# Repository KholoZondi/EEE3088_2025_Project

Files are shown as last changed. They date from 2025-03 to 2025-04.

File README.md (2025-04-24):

The repo stores all the shared work between EEE3088F Group 58 members Kholofelo Zondi and Max Mendelow for the Micro-mouse project project 2025. 

This includes the datasheets for certain ICs, past designs, general personal notes, downloaded schematics and the final design with Gerber and production files.

For the final design of the power subsystem, please navigate to "Micro_mouse_circuit/Micro_mouse_final" and consider the contents of the folder "Micro_mouse final" 
as the final design as of April 9th 2025. 

Full names and student numbers
Kholofelo Zondi ZNDKHO003
Max Mendelow MNDMAX003

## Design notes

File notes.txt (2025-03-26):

general q's:
where are the drill holes?
	-all the yellow filled circles

what input are we getting since motors are bidirectional
are the auxillary motors for steering
	-they are currently immaginary. For the time being, we will only be physically connecting 2 motos but we are adding in the capacity to connect 2 more future motors

clarrify requirement 7, 3v3 in?
	-similar to breadboard power sub system - just need to provide output 	pins

report:
block diagram: transfer behaviour shown in blocks and signals ( 3v3 input, DC ) shown with lines 

interface diagram: analogous to programming: shows what are data types passed into and out of function
with hardware - need to show what voltages go in and out, what signals, etc

bread board memo:

boost converter since linear voltage regulators have a minimum input that they regulate from

each motor has 2 physical connectors

check if A0,A1 addresses are correct based on master slave relation
are our board economic for preffered

battery - ina - charg - switch - rest of circuit

2 states: On+charge | off+charge

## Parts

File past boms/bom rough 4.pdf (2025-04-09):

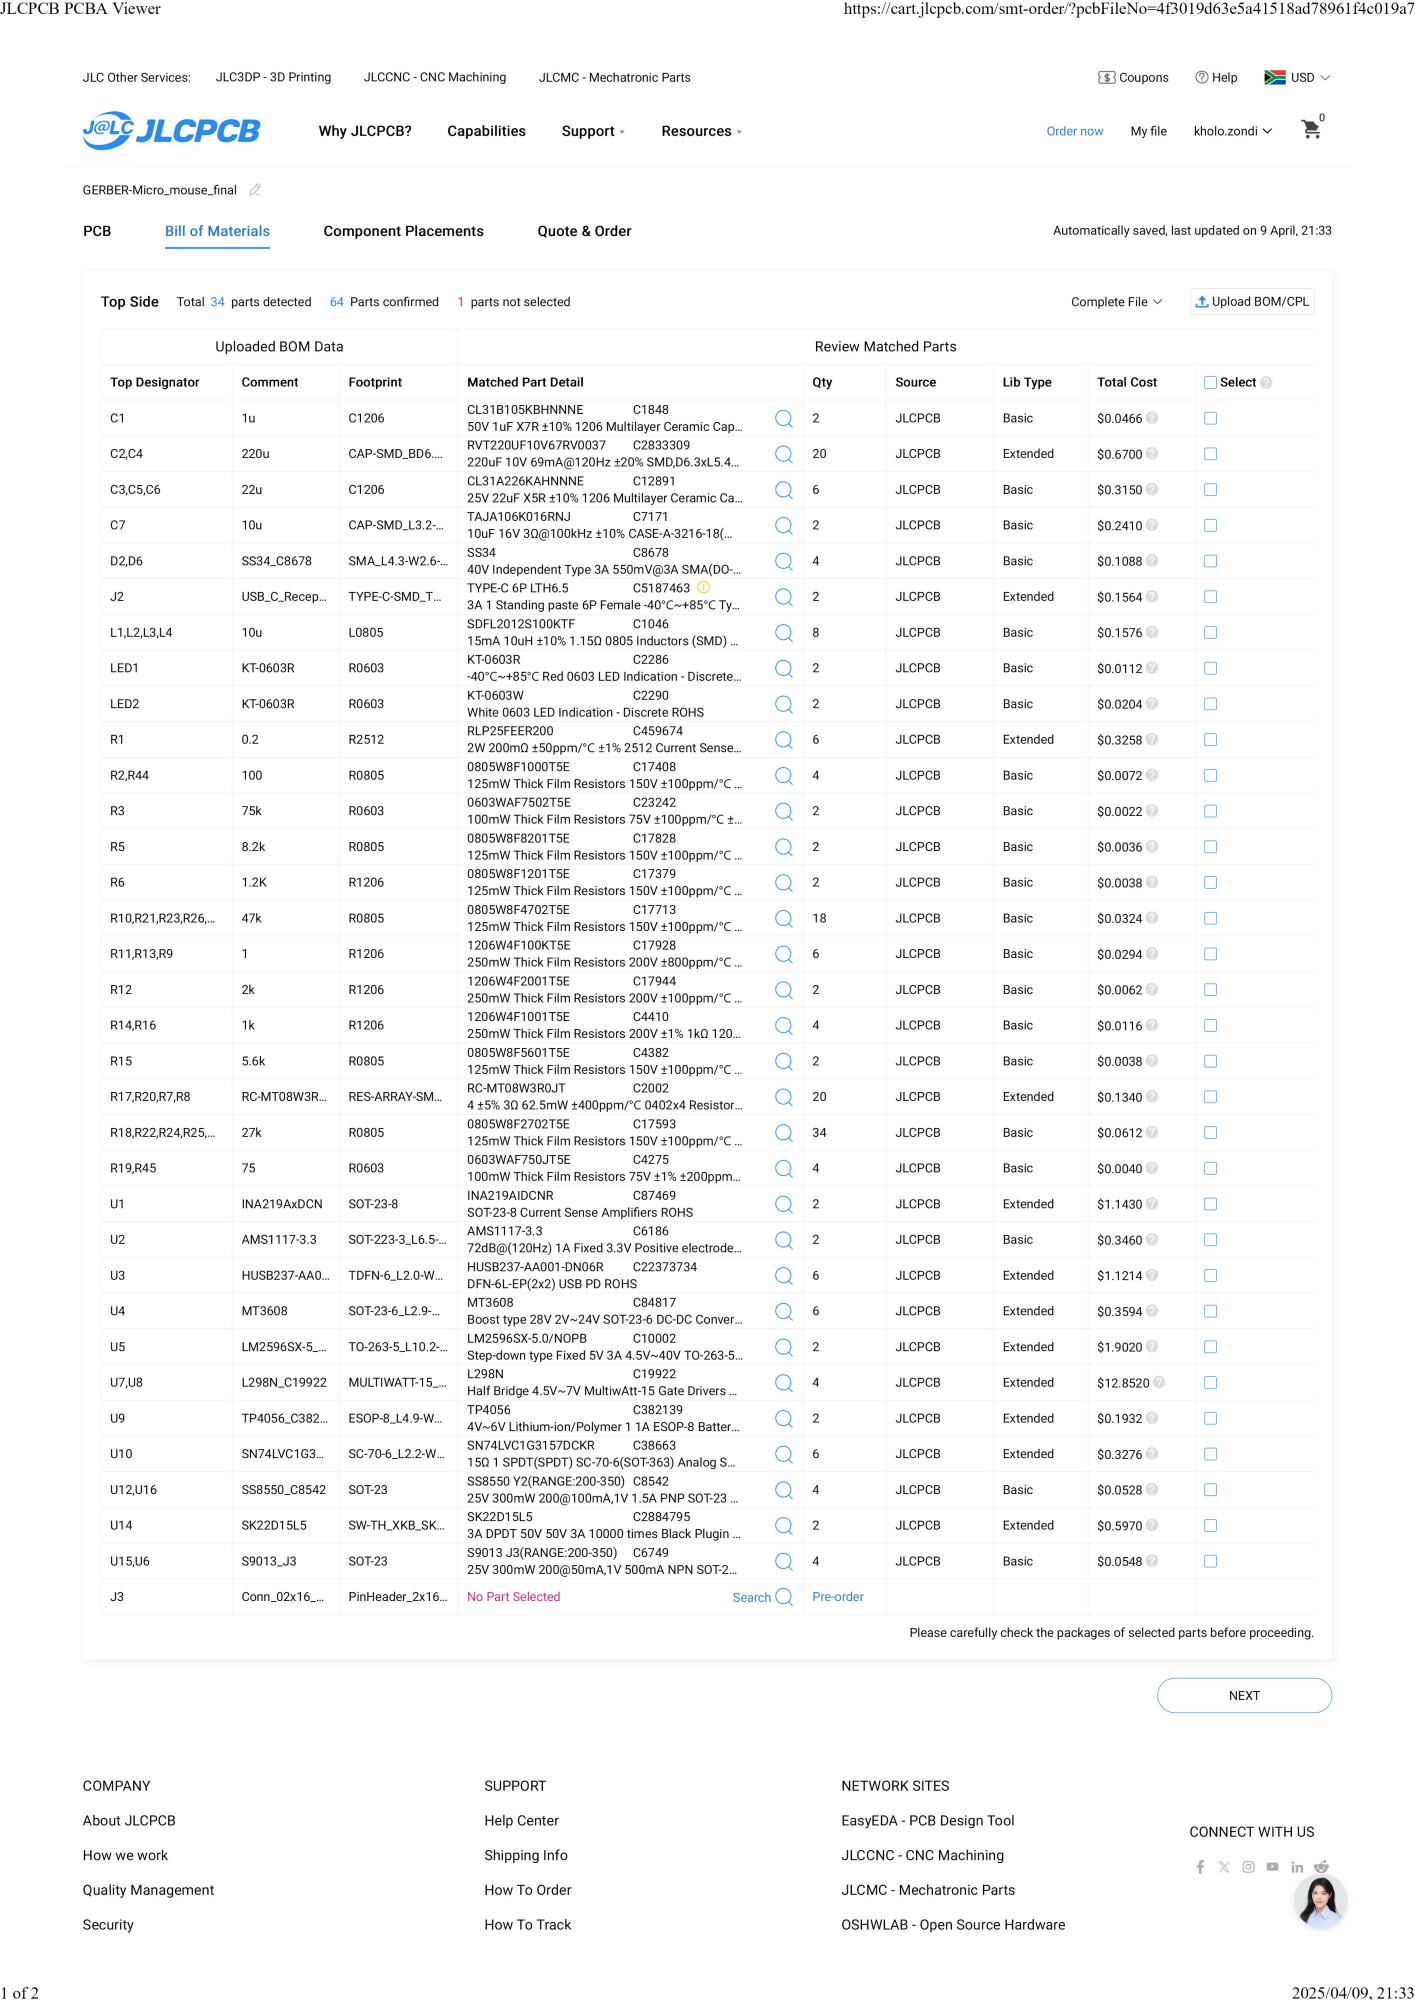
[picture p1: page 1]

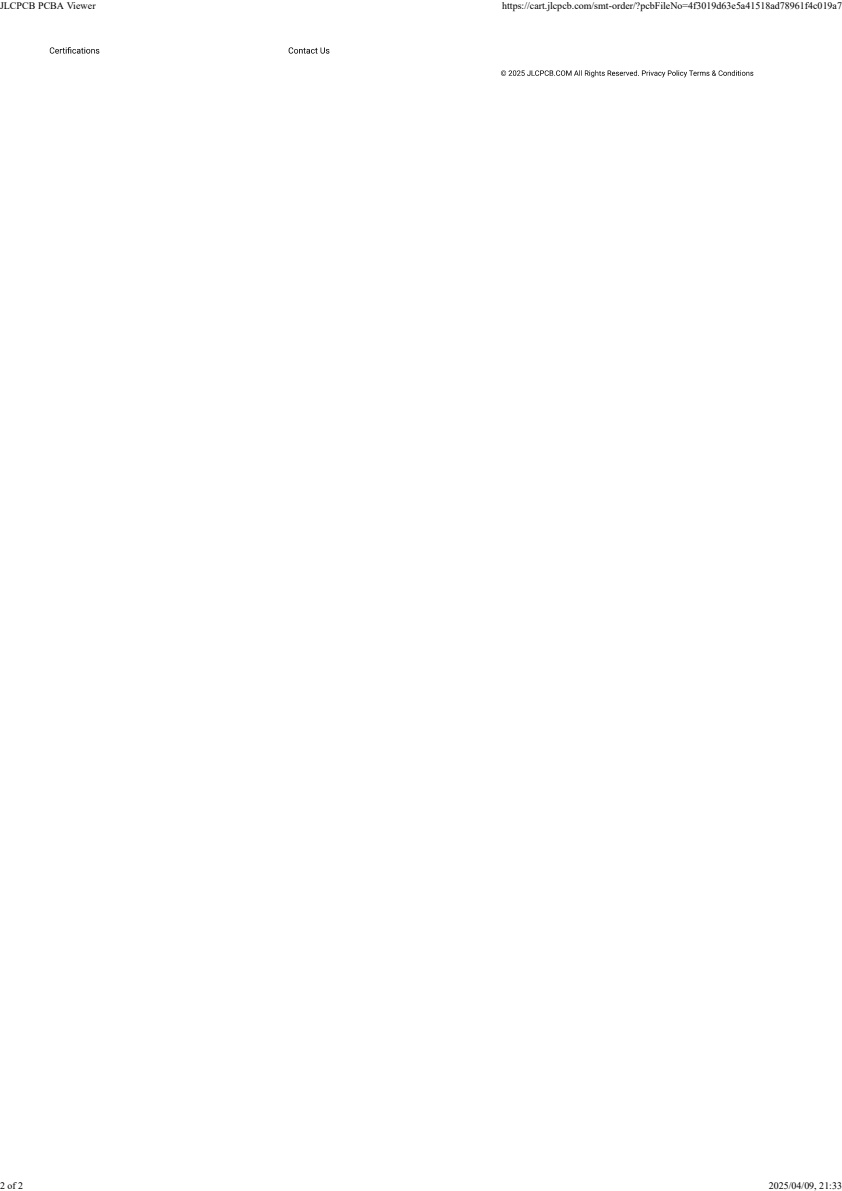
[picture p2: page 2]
JLCPCB PCBA Viewer; https://cart.jlcpcb.com/smt-order/?pcbFileNo=4f3019d63e5a41518ad78961f4c019a7

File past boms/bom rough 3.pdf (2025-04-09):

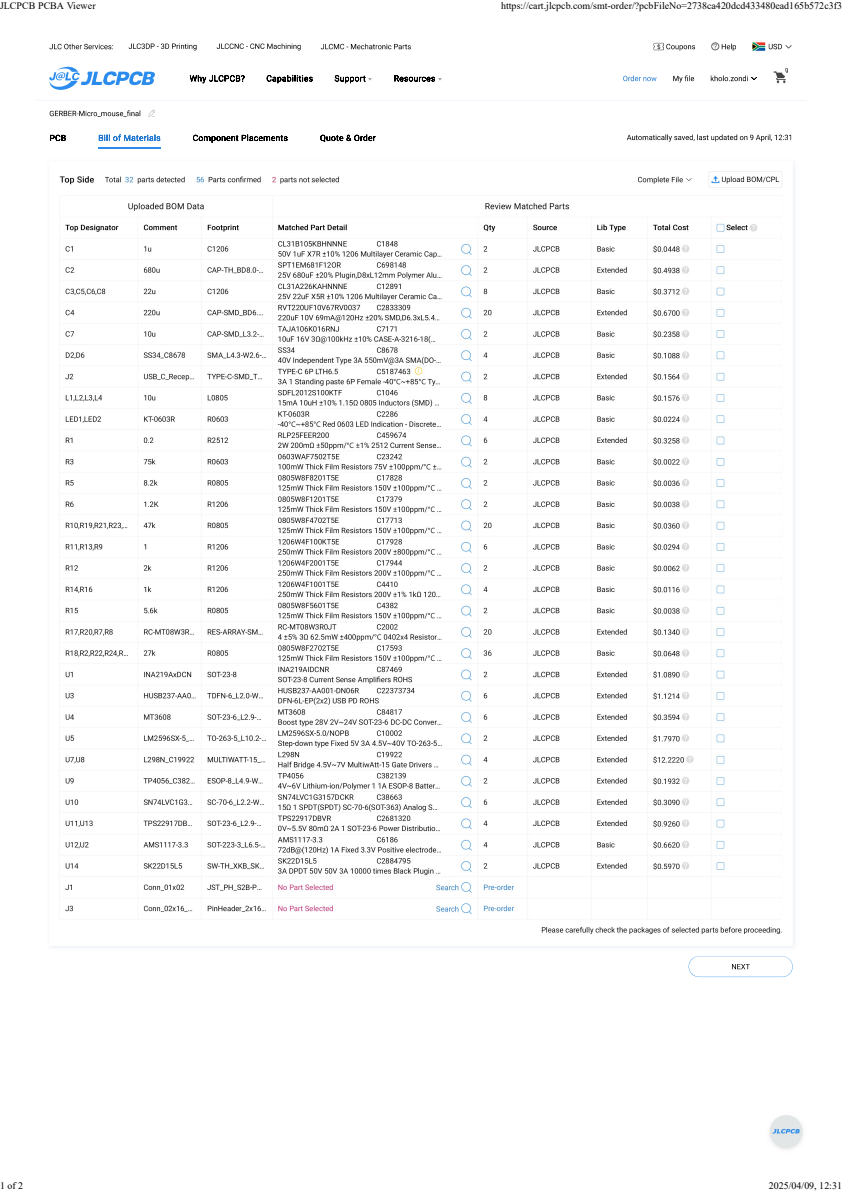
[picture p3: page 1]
JLCPCB PCBA Viewer; https://cart.jlcpcb.com/smt-order/?pcbFileNo=2738ca420dcd433480ead165b572c3f3

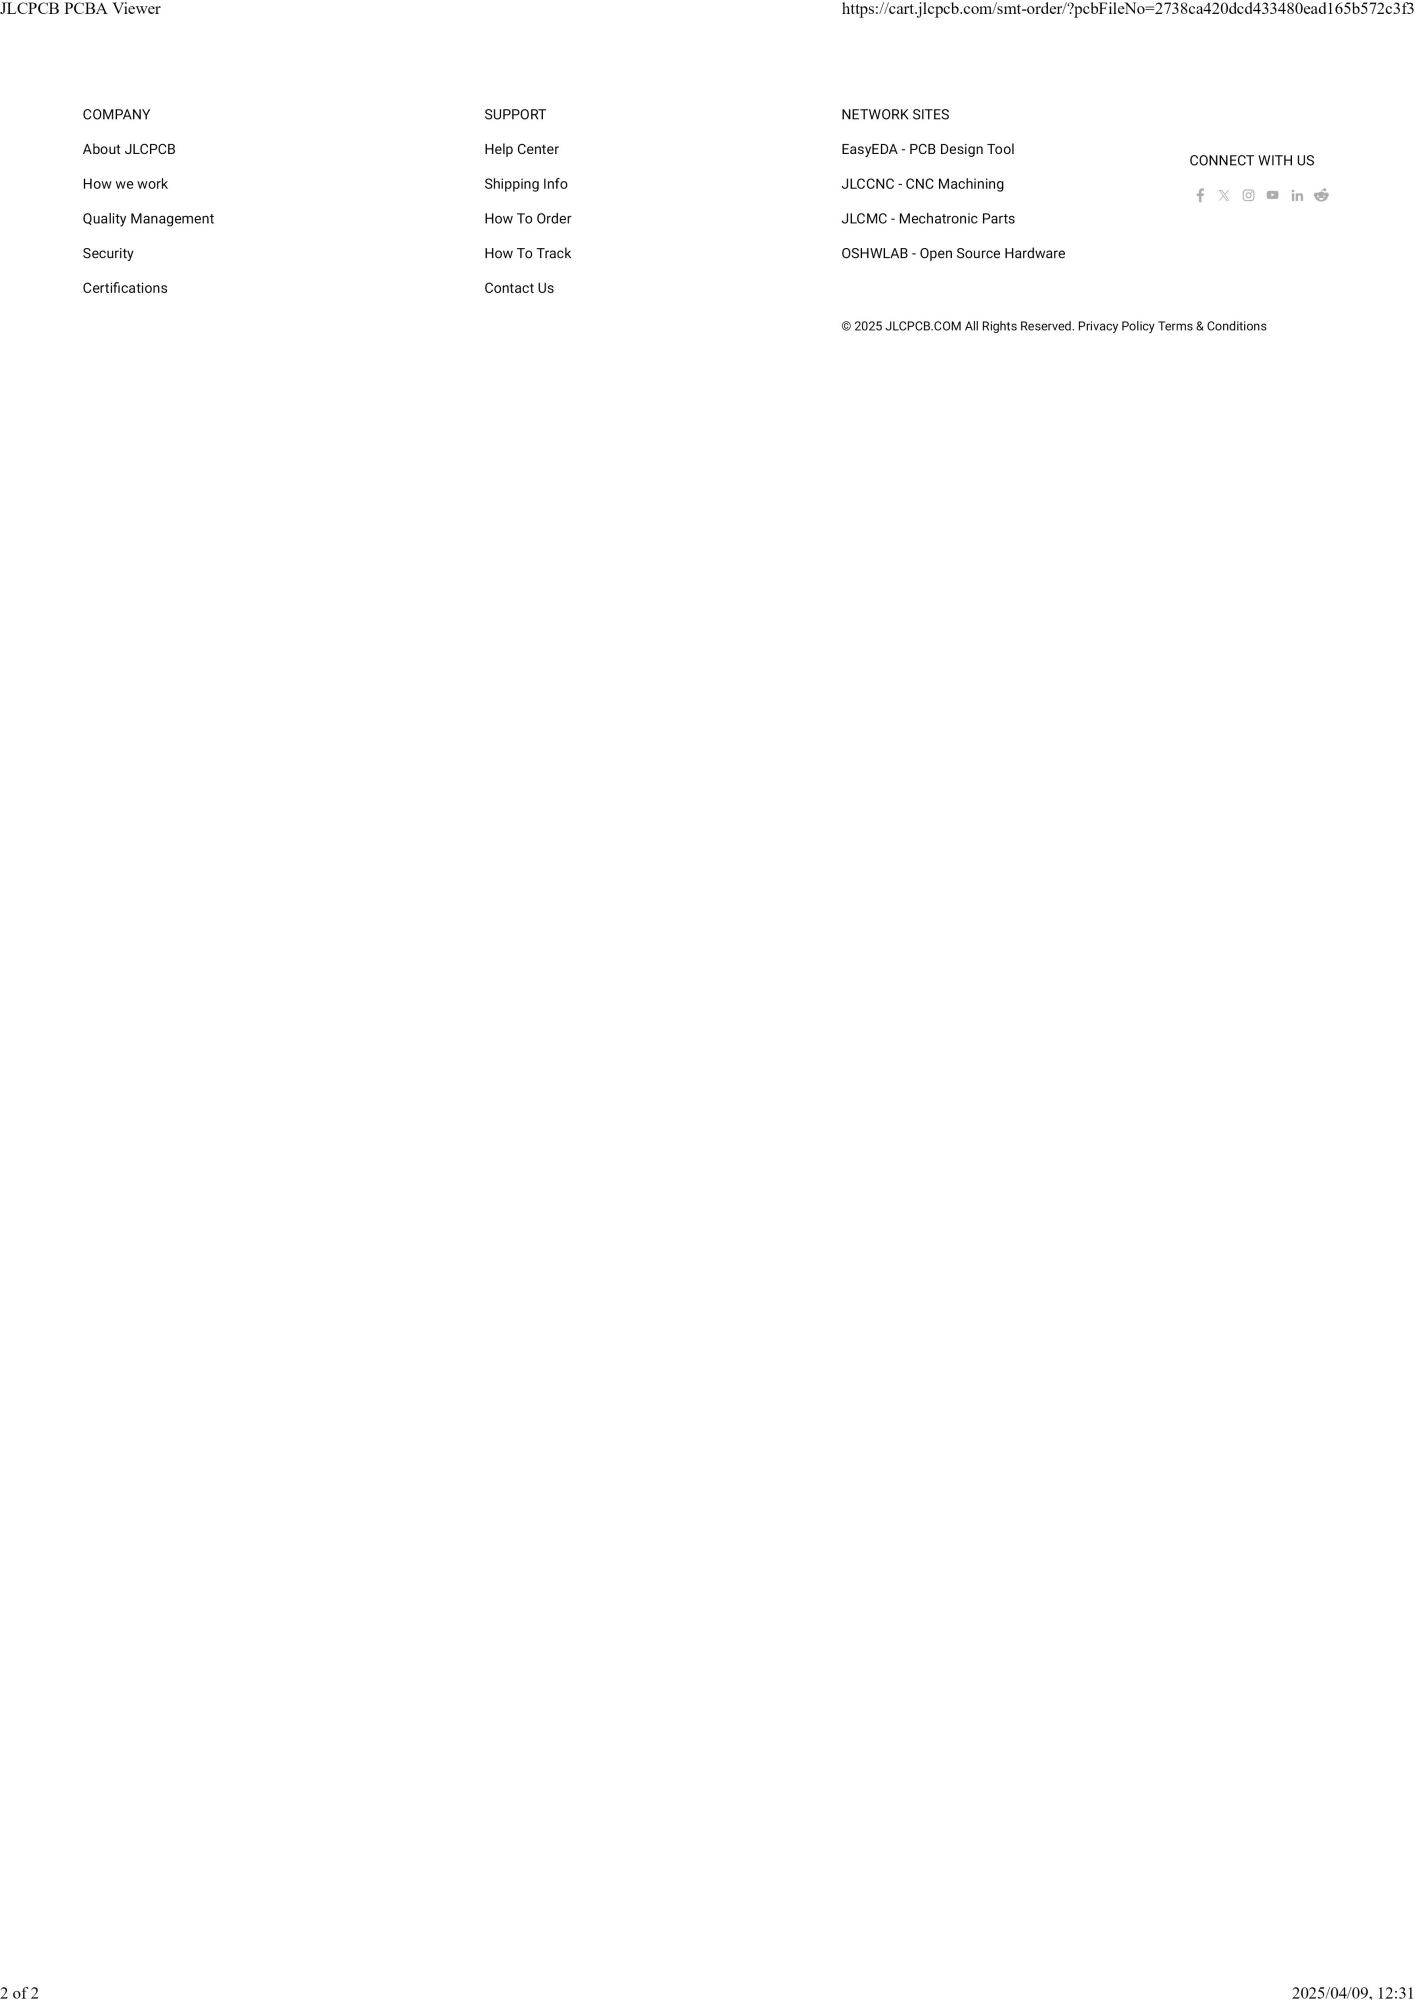
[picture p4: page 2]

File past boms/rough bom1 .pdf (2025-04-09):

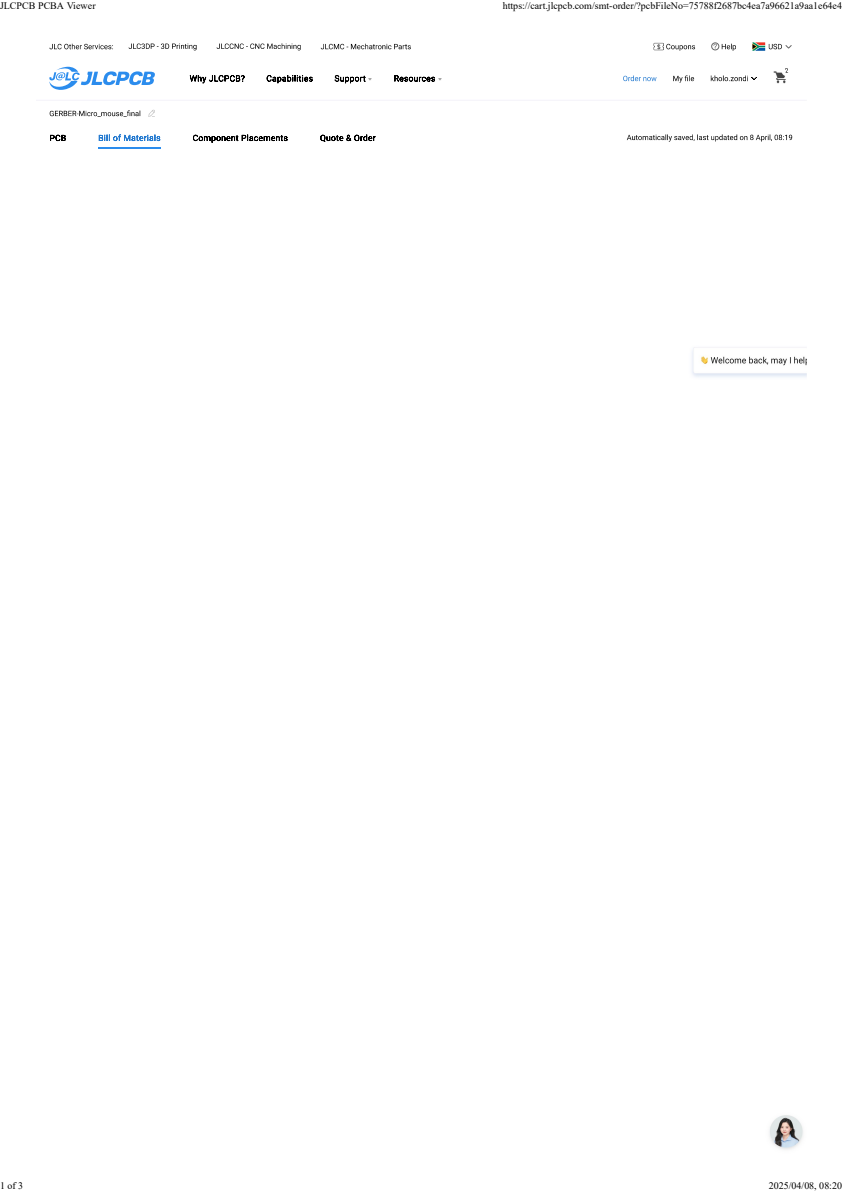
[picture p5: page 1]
JLCPCB PCBA Viewer; https://cart.jlcpcb.com/smt-order/?pcbFileNo=75788f2687bc4ea7a96621a9aa1e64e4

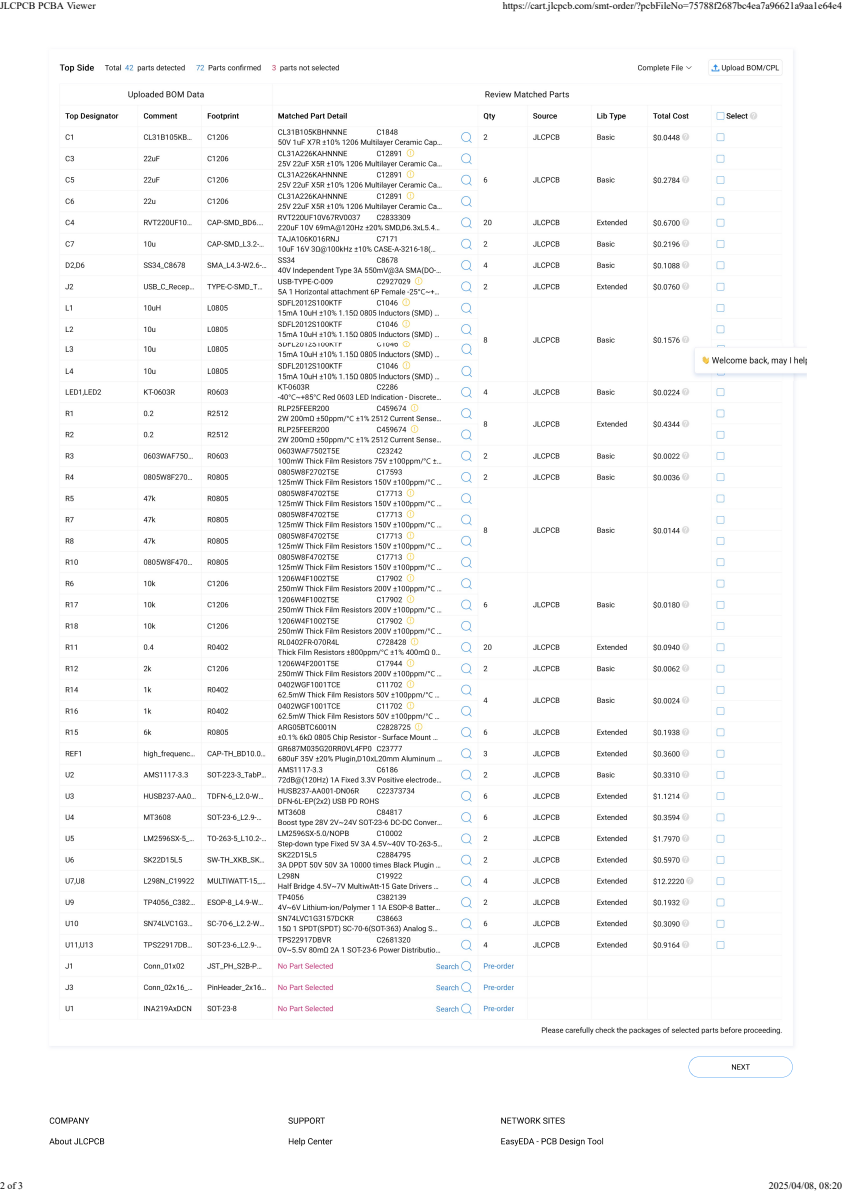
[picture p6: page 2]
JLCPCB PCBA Viewer; https://cart.jlcpcb.com/smt-order/?pcbFileNo=75788f2687bc4ea7a96621a9aa1e64e4

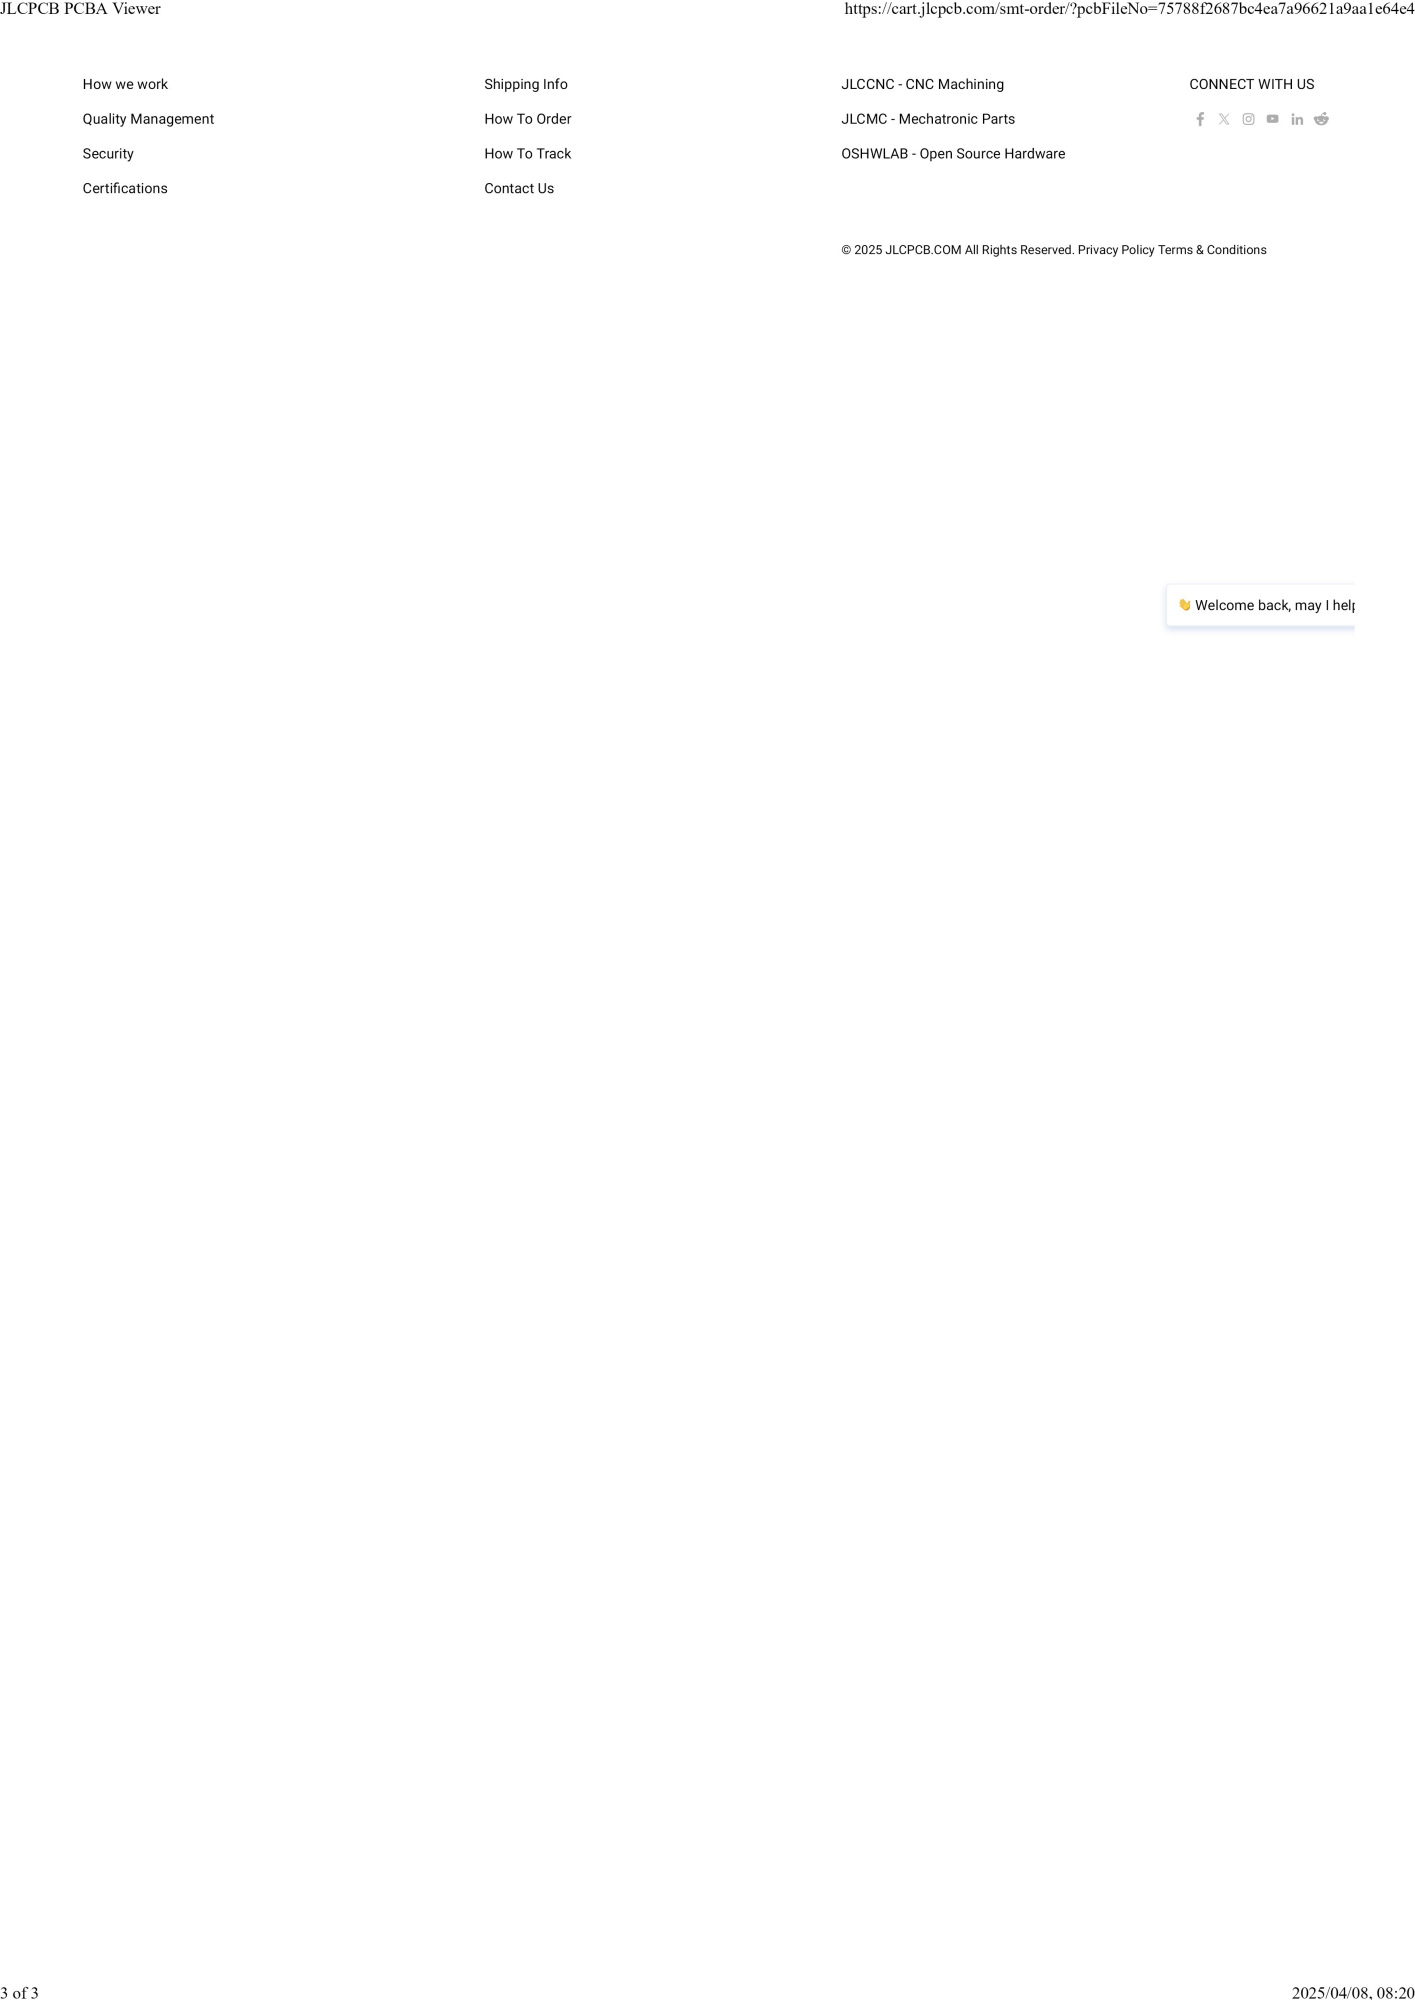
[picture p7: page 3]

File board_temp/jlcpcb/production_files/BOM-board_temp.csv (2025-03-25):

Comment | Designator | Footprint | LCSC | Quantity
IP2721 | U1 | TSSOP-16_4.4x5mm_P0.65mm |  | 1

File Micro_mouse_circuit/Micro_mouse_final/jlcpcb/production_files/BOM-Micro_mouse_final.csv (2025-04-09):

Comment | Designator | Footprint | LCSC | Quantity
LM2596SX-5_0/NOPB | U5 | TO-263-5_L10.2-W8.9-P1.70-TL | C10002 | 1
10u | L1,L2,L3,L4 | L0805 | C1046 | 4
22u | C3,C5,C6 | C1206 | C12891 | 3
1.2K | R6 | R1206 | C17379 | 1
100 | R2,R44 | R0805 | C17408 | 2
27k | R18,R22,R24,R25,R27,R28,R30,R31,R33,R34,R36,R37,R39,R4,R40,R42,R43 | R0805 | C17593 | 17
47k | R10,R21,R23,R26,R29,R32,R35,R38,R41 | R0805 | C17713 | 9
8.2k | R5 | R0805 | C17828 | 1
1 | R11,R13,R9 | R1206 | C17928 | 3
2k | R12 | R1206 | C17944 | 1
1u | C1 | C1206 | C1848 | 1
L298N_C19922 | U7,U8 | MULTIWATT-15_L19.6-W5.0-P1.27-L | C19922 | 2
RC-MT08W3R0JT | R17,R20,R7,R8 | RES-ARRAY-SMD_0402-8P-L2.0-W1.0-BL | C2002 | 4
HUSB237-AA001-DN06R | U3 | TDFN-6_L2.0-W2.0-P0.65-TL-EP | C22373734 | 1
KT-0603R | LED1 | R0603 | C2286 | 1
KT-0603R | LED2 | R0603 | C2290 | 1
75k | R3 | R0603 | C23242 | 1
220u | C2,C4 | CAP-SMD_BD6.3-L6.6-W6.6-FD | C2833309 | 2
SK22D15L5 | U14 | SW-TH_XKB_SK22D15L7 | C2884795 | 1
TP4056_C382139 | U9 | ESOP-8_L4.9-W3.9-P1.27-LS6.0-BL-EP | C382139 | 1
SN74LVC1G3157DCKR | U10 | SC-70-6_L2.2-W1.3-P0.65-LS2.1-BR | C38663 | 1
75 | R19,R45 | R0603 | C4275 | 2
5.6k | R15 | R0805 | C4382 | 1
1k | R14,R16 | R1206 | C4410 | 2
0.2 | R1 | R2512 | C459674 | 1
USB_C_Receptacle_PowerOnly_6P | J2 | TYPE-C-SMD_TYPE-C-6P | C5187463 | 1
AMS1117-3.3 | U2 | SOT-223-3_L6.5-W3.4-P2.30-LS7.0-BR | C6186 | 1
S9013_J3 | U15,U6 | SOT-23 | C6749 | 2
10u | C7 | CAP-SMD_L3.2-W1.6-RD-C7171 | C7171 | 1
MT3608 | U4 | SOT-23-6_L2.9-W1.6-P0.95-LS2.8-BL | C84817 | 1
SS8550_C8542 | U12,U16 | SOT-23 | C8542 | 2
SS34_C8678 | D2,D6 | SMA_L4.3-W2.6-LS5.2-RD | C8678 | 2
INA219AxDCN | U1 | SOT-23-8 | C87469 | 1
Conn_02x16_Odd_Even | J3 | PinHeader_2x16_P2.54mm_Vertical |  | 1
TestPoint_2Pole | TP8 | TestPoint_2Pads_Pitch2.54mm_Drill0.8mm |  | 1
TestPoint_2Pole | TP6 | TestPoint_2Pads_Pitch2.54mm_Drill0.8mm |  | 1
TestPoint | TP1 | TestPoint_Pad_2.5x2.5mm |  | 1
TestPoint_2Pole | TP10 | TestPoint_2Pads_Pitch2.54mm_Drill0.8mm |  | 1
TestPoint_2Pole | TP3 | TestPoint_2Pads_Pitch2.54mm_Drill0.8mm |  | 1
TestPoint | TP18 | TestPoint_Pad_2.5x2.5mm |  | 1
TestPoint | TP17 | TestPoint_Pad_2.5x2.5mm |  | 1
TestPoint | TP16 | TestPoint_Pad_2.5x2.5mm |  | 1
TestPoint | TP15 | TestPoint_Pad_2.5x2.5mm |  | 1
TestPoint | TP14 | TestPoint_Pad_2.5x2.5mm |  | 1
TestPoint | TP13 | TestPoint_Pad_2.5x2.5mm |  | 1
TestPoint | TP12 | TestPoint_Pad_2.5x2.5mm |  | 1
TestPoint | TP11 | TestPoint_Pad_2.5x2.5mm |  | 1
TestPoint_2Pole | TP5 | TestPoint_2Pads_Pitch2.54mm_Drill0.8mm |  | 1
TestPoint_2Pole | TP4 | TestPoint_2Pads_Pitch2.54mm_Drill0.8mm |  | 1
TestPoint | TP20 | TestPoint_Pad_2.5x2.5mm |  | 1
TestPoint | TP19 | TestPoint_Pad_2.5x2.5mm |  | 1

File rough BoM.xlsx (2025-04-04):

Secction |  |  |  |  |  | most likely needed
battery |  |  |  |  |  | boost converter (battery)
requirement | component | model # | base cost (USD) | extended? (+$3) | link (JLC) | linear regulator (battery) (type LDO)
2 | INA219 | INA219AIDCNR | 0.5955 | 3 | https://jlcpcb.com/partdetail/TexasInstruments-INA219AIDCNR/C87469 | h bridge IC (motors)
5 | USB C header /6b | TYPE-C 6P LTH6.5 | 0.0782 | 3 | https://jlcpcb.com/partdetail/ShouHan-TYPE_C_6P_LTH65/C5187463 | usb type c header (battery) | + usb type c pd (battery)
5 | USB C PD | HUSB237 | 0.19 | 3 | https://jlcpcb.com/partdetail/Hynetek-HUSB237_AA001DN06R/C22373734 | INA219 (battery)
3,4 | Charging | TP4056 | 0.09 | 3 | https://jlcpcb.com/partdetail/TPOWER-TP4056/C382139 | Li battery charger
3,4 | Buck dc-dc | LM2596SX-5.0/NOPB | 0.9135 | 0 | https://jlcpcb.com/partdetail/TexasInstruments-LM2596SX_5_0NOPB/C10002
4 | analog switch | SN74LVC1G3157DCKR | 0.0513 | 3 | https://jlcpcb.com/partdetail/TexasInstruments-SN74LVC1G3157DCKR/C38663
2 | shunt resistor | RLP25FEER200 | 0.05 | 3 | https://jlcpcb.com/partdetail/ta_iTech-RLP25FEER200/C459674
Discrete components
 | cap (5V boosted) | CL31A226KAHNNNE |  | 0 | https://jlcpcb.com/partdetail/13537-CL31A226KAHNNNE/C12891
 | 10k resistor | 1206W4F1002T5E |  | 0 | https://jlcpcb.com/partdetail/18590-1206W4F1002T5E/C17902
Sub-total |  |  | 19.9685
Motors
requirement | component | model # | cost (USD) | extended? (+$3) | link (JLC)
8 | On/Off switch | SK22D15L5 | 0.31 | 3 | https://jlcpcb.com/partdetail/XkbConnection-SK22D15L5/C2884795
 | 5V out | MT3608 | 0.06 | 3 | https://jlcpcb.com/partdetail/xi_an_AerosemiTech-MT3608/C84817
Sub-total |  |  | 6.37
Total |  |  | 26.3385
Budget |  |  | 56.5
Left over |  |  | 30.1615

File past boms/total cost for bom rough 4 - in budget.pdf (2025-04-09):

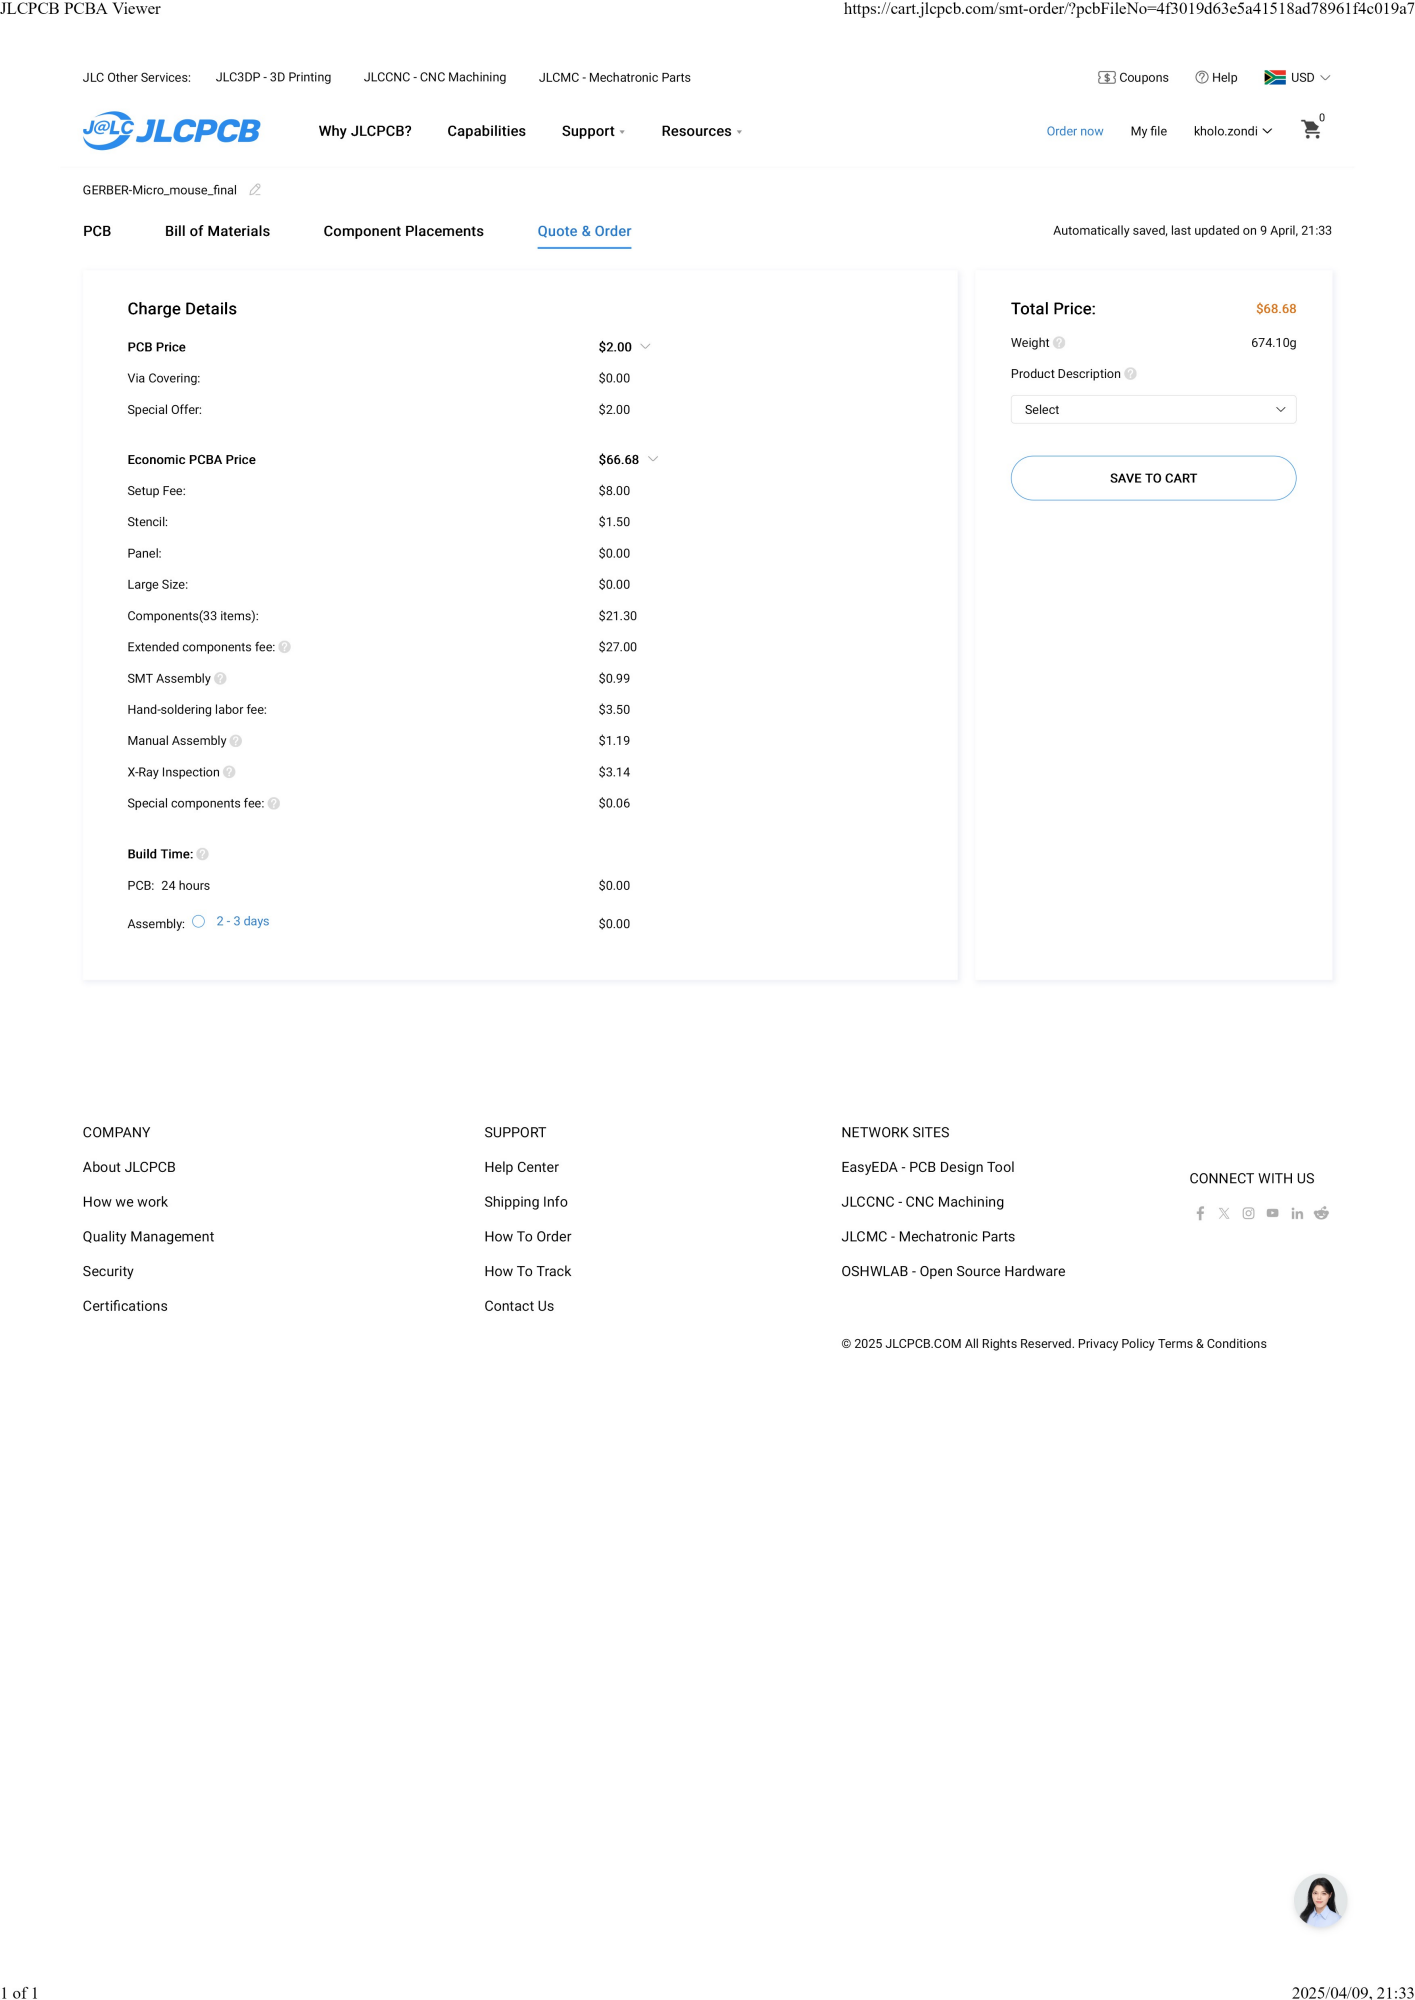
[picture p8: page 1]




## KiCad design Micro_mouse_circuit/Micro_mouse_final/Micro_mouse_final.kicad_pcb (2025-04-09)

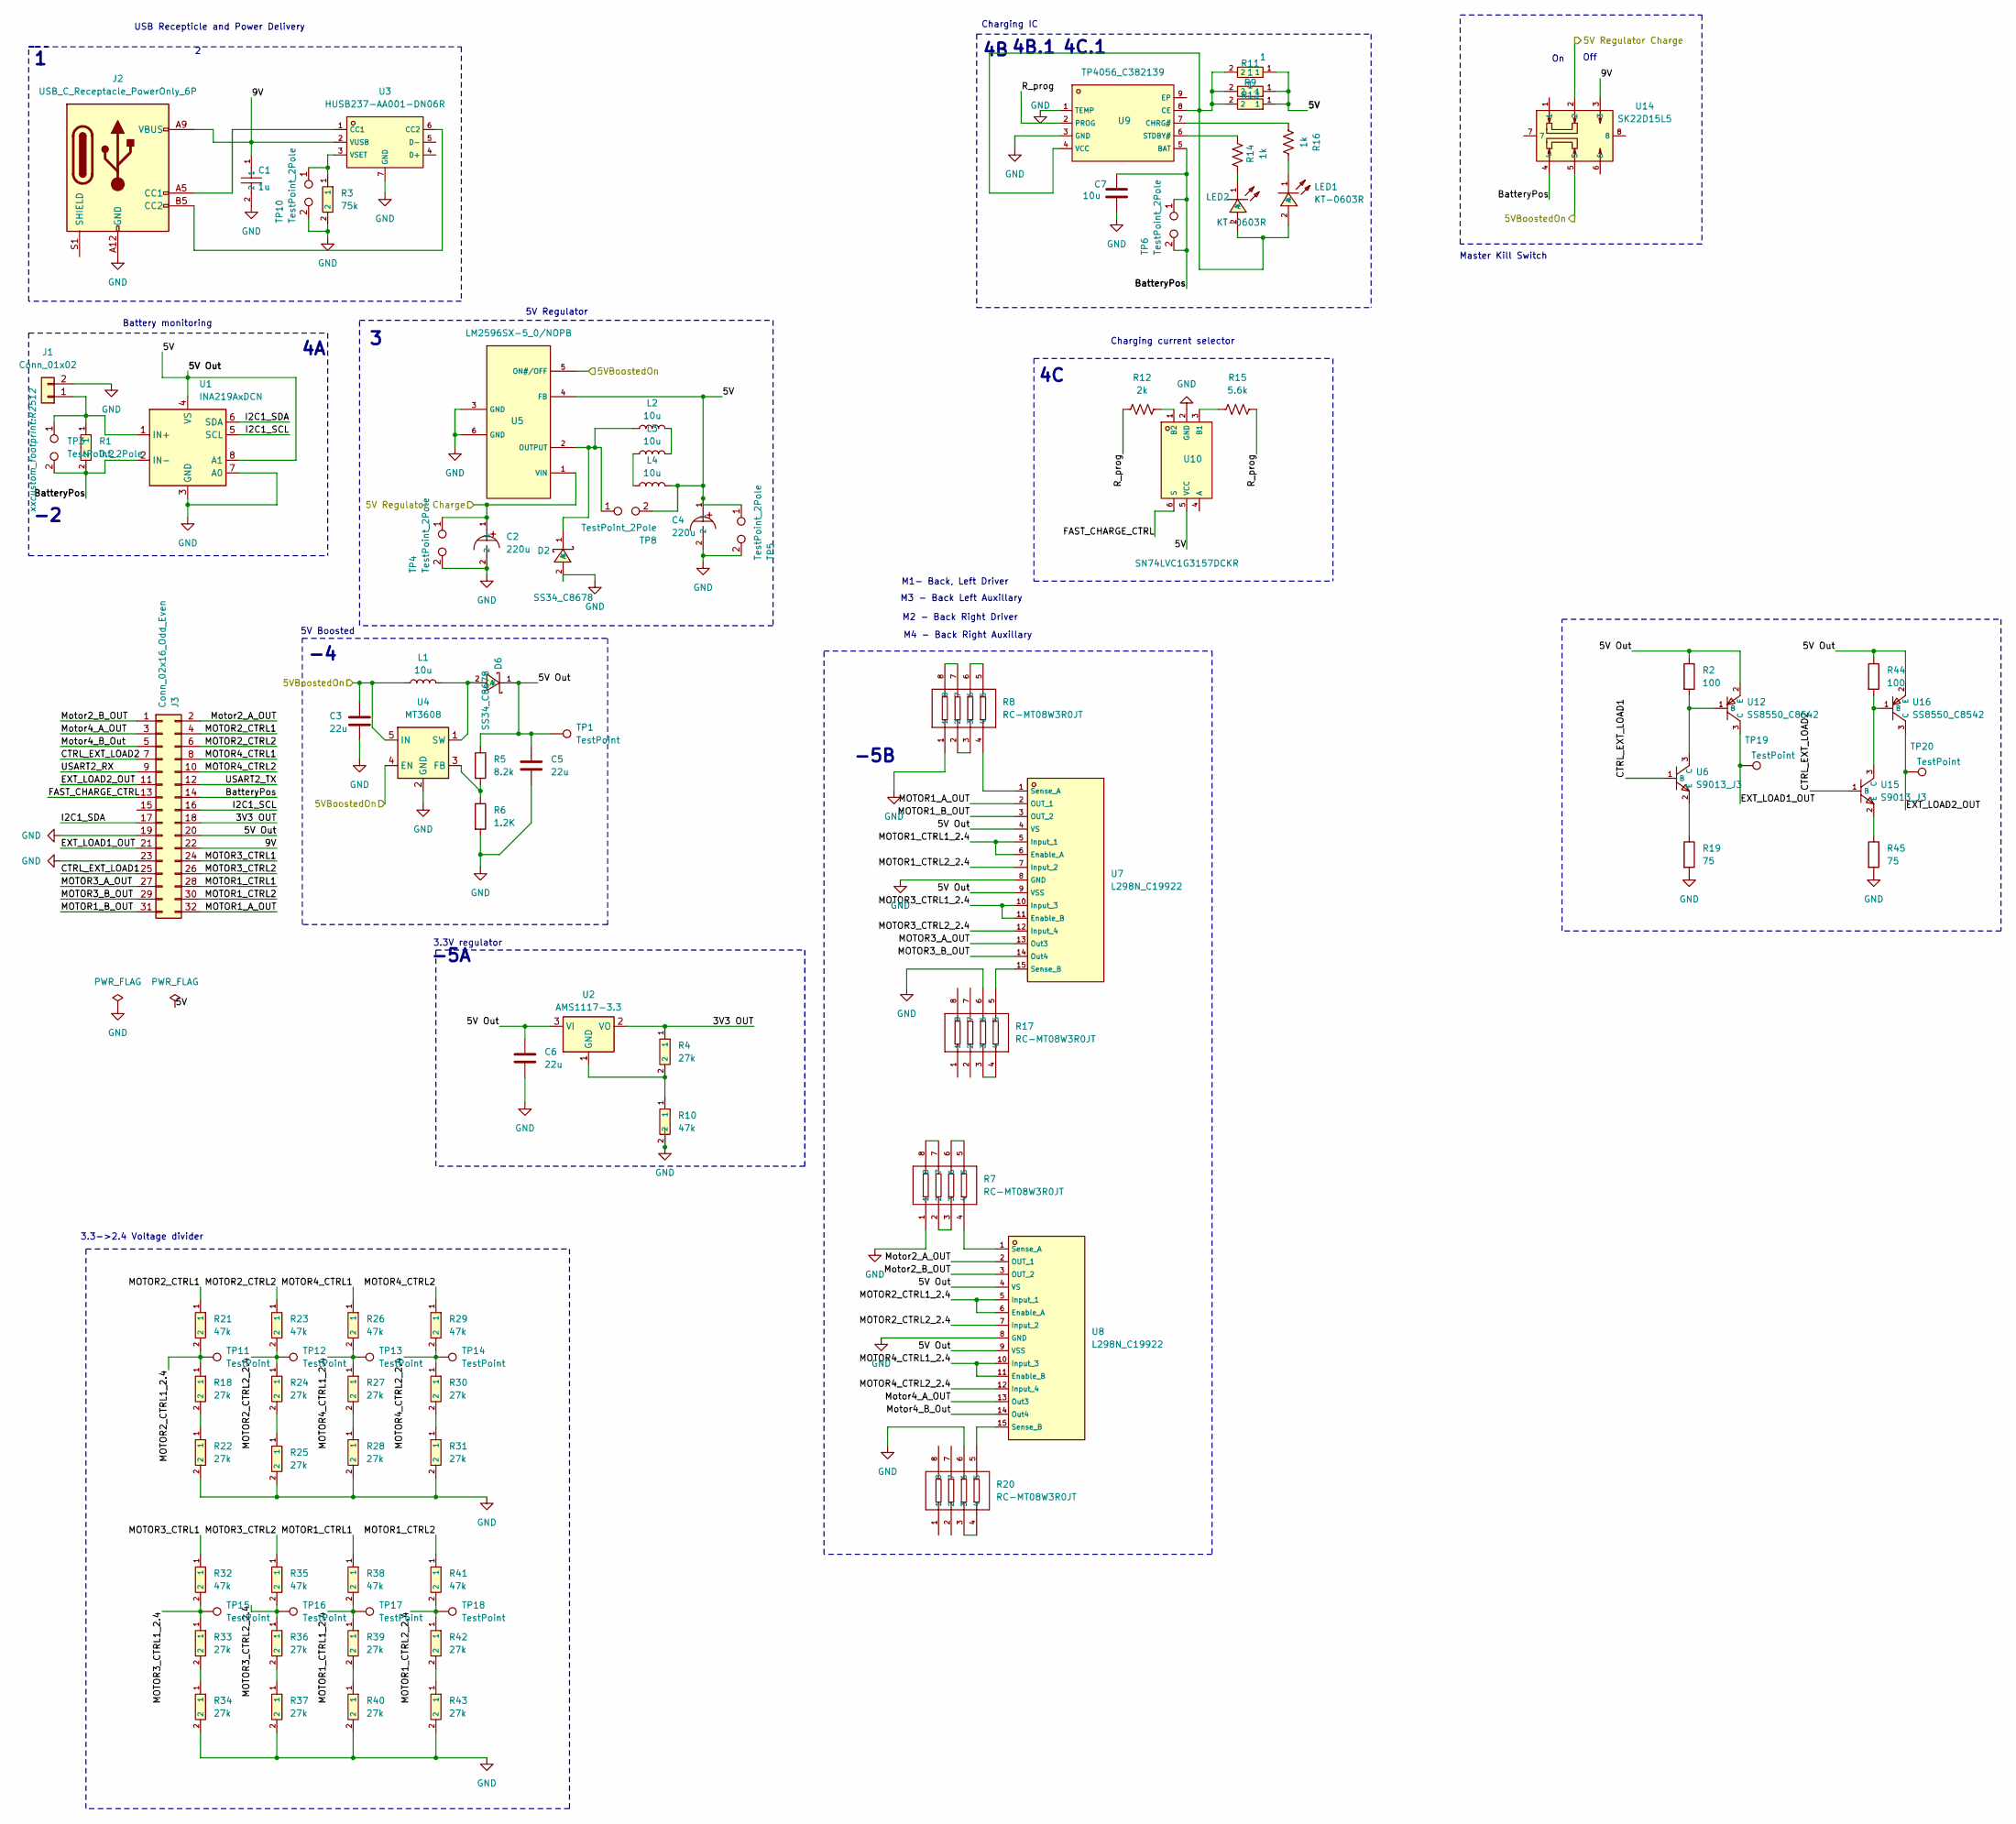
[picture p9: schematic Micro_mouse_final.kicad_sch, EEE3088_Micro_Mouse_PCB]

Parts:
C1: 1u; C1206; LCSC C1848
C2, C4: 220u; CAP-SMD_BD6.3-L6.6-W6.6-FD; LCSC C2833309
C3, C5, C6: 22u; C1206
C7: 10u; CAP-SMD_L3.2-W1.6-RD-C7171; LCSC C7171
D2, D6: SS34_C8678; SMA_L4.3-W2.6-LS5.2-RD; LCSC C8678
J1: Conn_01x02; JST_PH_S2B-PH-K_1x02_P2.00mm_Horizontal
J2: USB_C_Receptacle_PowerOnly_6P; TYPE-C-SMD_TYPE-C-6P; LCSC C5187463
J3: Conn_02x16_Odd_Even; PinHeader_2x16_P2.54mm_Vertical
L1, L2, L3, L4: 10u; L0805; LCSC C1046
LED1: KT-0603R; R0603; LCSC C2286
LED2: KT-0603R; R0603; LCSC C2290
R1: 0.2; R2512; LCSC C459674
R2, R44: 100; R0805; LCSC C17408
R3: 75k; R0603; LCSC C23242
R4, R18, R22, R24, R25, R27, R28, R30, R31, R33, R34, R36, R37, R39, R40, R42, R43: 27k; R0805; LCSC C17593
R5: 8.2k; R0805; LCSC C17828
R6: 1.2K; R1206; LCSC C17379
R7, R8, R17, R20: RC-MT08W3R0JT; RES-ARRAY-SMD_0402-8P-L2.0-W1.0-BL; LCSC C2002
R9, R11, R13: 1; R1206; LCSC C17928
R10, R21, R23, R26, R29, R32, R35, R38, R41: 47k; R0805; LCSC C17713
R12: 2k; R1206; LCSC C17944
R14, R16: 1k; R1206; LCSC C4410
R15: 5.6k; R0805; LCSC C4382
R19, R45: 75; R0603; LCSC C4275
TP1, TP11, TP12, TP13, TP14, TP15, TP16, TP17, TP18, TP19, TP20: TestPoint; TestPoint_Pad_2.5x2.5mm
TP3, TP4, TP5, TP6, TP8, TP10: TestPoint_2Pole; TestPoint_2Pads_Pitch2.54mm_Drill0.8mm
U1: INA219AxDCN; SOT-23-8; LCSC C87469
U2: AMS1117-3.3; SOT-223-3_L6.5-W3.4-P2.30-LS7.0-BR; LCSC C6186
U3: HUSB237-AA001-DN06R; TDFN-6_L2.0-W2.0-P0.65-TL-EP; LCSC C22373734
U4: MT3608; SOT-23-6_L2.9-W1.6-P0.95-LS2.8-BL; LCSC C84817
U5: LM2596SX-5_0/NOPB; TO-263-5_L10.2-W8.9-P1.70-TL; LCSC C10002
U6, U15: S9013_J3; SOT-23; LCSC C6749
U7, U8: L298N_C19922; MULTIWATT-15_L19.6-W5.0-P1.27-L; LCSC C19922
U9: TP4056_C382139; ESOP-8_L4.9-W3.9-P1.27-LS6.0-BL-EP; LCSC C382139
U10: SN74LVC1G3157DCKR; SC-70-6_L2.2-W1.3-P0.65-LS2.1-BR; LCSC C38663
U12, U16: SS8550_C8542; SOT-23; LCSC C8542
U14: SK22D15L5; SW-TH_XKB_SK22D15L7; LCSC C2884795

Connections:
/3V3 OUT: J3.18, R4.1, U2.2 (VO)
/5V: C4.1, C5.1, C6.1, D6.1 (K), J3.20, L4.2, R2.1, R5.1, R9.1, R11.1, R13.1, R44.1, TP1.1, TP5.1, TP8.2, U1.4 (VS), U1.8 (A1), U2.3 (VI), U5.4 (FB), U7.4 (VS), U7.9 (VSS), U8.4 (VS), U8.9 (VSS), U10.5 (VCC), U12.2 (E), U16.2 (E)
/5V Regulator Charge: C2.1, TP4.1, U5.1 (VIN), U14.2
/5VBoostedOn: C3.1, L1.1, U4.4 (EN), U4.5 (IN), U5.5 (ON#/OFF), U14.5
/9V: C1.1, J2.A9 (VBUS), J2.B9 (VBUS), J3.22, U3.2 (VUSB), U14.3
/BatteryPos: C7.1, J3.14, R1.2, TP3.2, TP6.1, TP6.2, U1.2 (IN-), U9.5 (BAT), U14.4
/CTRL_EXT_LOAD1: J3.25, U6.1 (B)
/CTRL_EXT_LOAD2: J3.7, U15.1 (B)
/EXT_LOAD1_OUT: J3.21, TP19.1, U12.3 (C)
/EXT_LOAD2_OUT: J3.11, TP20.1, U16.3 (C)
/FAST_CHARGE_CTRL: J3.13, U10.6 (S)
/I2C1_SCL: J3.16, U1.5 (SCL)
/I2C1_SDA: J3.17, U1.6 (SDA)
/MOTOR1_A_OUT: J3.32, U7.2 (OUT_1)
/MOTOR1_B_OUT: J3.31, U7.3 (OUT_2)
/MOTOR1_CTRL1: J3.28, R38.1
/MOTOR1_CTRL1_2.4: R38.2, R39.1, TP17.1, U7.5 (Input_1), U7.6 (Enable_A)
/MOTOR1_CTRL2: J3.30, R41.1
/MOTOR1_CTRL2_2.4: R41.2, R42.1, TP18.1, U7.7 (Input_2)
/MOTOR2_CTRL1: J3.4, R21.1
/MOTOR2_CTRL1_2.4: R18.1, R21.2, TP11.1, U8.5 (Input_1), U8.6 (Enable_A)
/MOTOR2_CTRL2: J3.6, R23.1
/MOTOR2_CTRL2_2.4: R23.2, R24.1, TP12.1, U8.7 (Input_2)
/MOTOR3_A_OUT: J3.27, U7.13 (Out3)
/MOTOR3_B_OUT: J3.29, U7.14 (Out4)
/MOTOR3_CTRL1: J3.24, R32.1
/MOTOR3_CTRL1_2.4: R32.2, R33.1, TP15.1, U7.10 (Input_3), U7.11 (Enable_B)
/MOTOR3_CTRL2: J3.26, R35.1
/MOTOR3_CTRL2_2.4: R35.2, R36.1, TP16.1, U7.12 (Input_4)
/MOTOR4_CTRL1: J3.8, R26.1
/MOTOR4_CTRL1_2.4: R26.2, R27.1, TP13.1, U8.10 (Input_3), U8.11 (Enable_B)
/MOTOR4_CTRL2: J3.10, R29.1
/MOTOR4_CTRL2_2.4: R29.2, R30.1, TP14.1, U8.12 (Input_4)
/Motor2_A_OUT: J3.2, U8.2 (OUT_1)
/Motor2_B_OUT: J3.1, U8.3 (OUT_2)
/Motor4_A_OUT: J3.3, U8.13 (Out3)
/Motor4_B_Out: J3.5, U8.14 (Out4)
/R_prog: R12.1, R15.1, U9.2 (PROG)
/USART2_RX: J3.9
/USART2_TX: J3.12
GND: C1.2, C2.2, C3.2, C4.2, C5.2, C6.2, C7.2, D2.2 (A), J1.2, J2.A12 (GND), J2.B12 (GND), J3.19, J3.23, R3.2, R6.2, R7.1, R8.1, R10.2, R17.6, R19.2, R20.6, R22.2, R25.2, R28.2, R31.2, R34.2, R37.2, R40.2, R43.2, R45.2, TP4.2, TP5.2, TP10.2, U1.3 (GND), U1.7 (A0), U3.7 (GND), U4.2 (GND), U5.3 (GND), U5.6 (GND), U7.8 (GND), U8.8 (GND), U9.1 (TEMP), U9.3 (GND), U10.2 (GND)
unnamed: D2.1 (K), L2.1, TP8.1, U5.2 (OUTPUT)
unnamed: D6.2 (A), L1.2, U4.1 (SW)
unnamed: J1.1, R1.1, TP3.1, U1.1 (IN+)
unnamed: J2.A5 (CC1), U3.1 (CC1)
unnamed: J2.B5 (CC2), U3.6 (CC2)
unnamed: L2.2, L3.2
unnamed: L3.1, L4.1
unnamed: LED1.2 (A), LED2.2 (A), R9.2, R11.2, R13.2, U9.4 (VCC), U9.8 (CE)
unnamed: LED1.1 (K), R16.1
unnamed: LED2.1 (K), R14.2
unnamed: R7.2, R7.3
unnamed: R7.5, R7.6
unnamed: R7.7, R7.8
unnamed: R8.2, R8.3
unnamed: R8.5, R8.6
unnamed: R8.7, R8.8
unnamed: R17.3, R17.4
unnamed: R18.2, R22.1
unnamed: R20.3, R20.4
unnamed: R24.2, R25.1
unnamed: R27.2, R28.1
unnamed: R30.2, R31.1
unnamed: R33.2, R34.1
unnamed: R36.2, R37.1
unnamed: R39.2, R40.1
unnamed: R42.2, R43.1
unnamed: R4.2, R10.1, U2.1 (GND)
unnamed: R3.1, TP10.1, U3.3 (VSET)
unnamed: R5.2, R6.1, U4.3 (FB)
unnamed: R19.1, U6.2 (E)
unnamed: R8.4, U7.1 (Sense_A)
unnamed: R17.5, U7.15 (Sense_B)
unnamed: R7.4, U8.1 (Sense_A)
unnamed: R20.5, U8.15 (Sense_B)
unnamed: R16.2, U9.7 (CHRG#)
unnamed: R14.1, U9.6 (STDBY#)
unnamed: R15.2, U10.3 (B1)
unnamed: R12.2, U10.1 (B2)
unnamed: R2.2, U6.3 (C), U12.1 (B)
unnamed: R44.2, U15.3 (C), U16.1 (B)
unnamed: R45.1, U15.2 (E)

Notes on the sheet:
5V Boosted
Charging current selector
4C.1
Battery monitoring
4B.1
M3 - Back Left Auxillary
Master Kill Switch
5V Regulator
Charging IC
-5A
Off
3.3->2.4 Voltage divider
-5B
M4 - Back Right Auxillary
M2 - Back Right Driver
3.3V regulator
USB Recepticle and Power Delivery
M1- Back, Left Driver

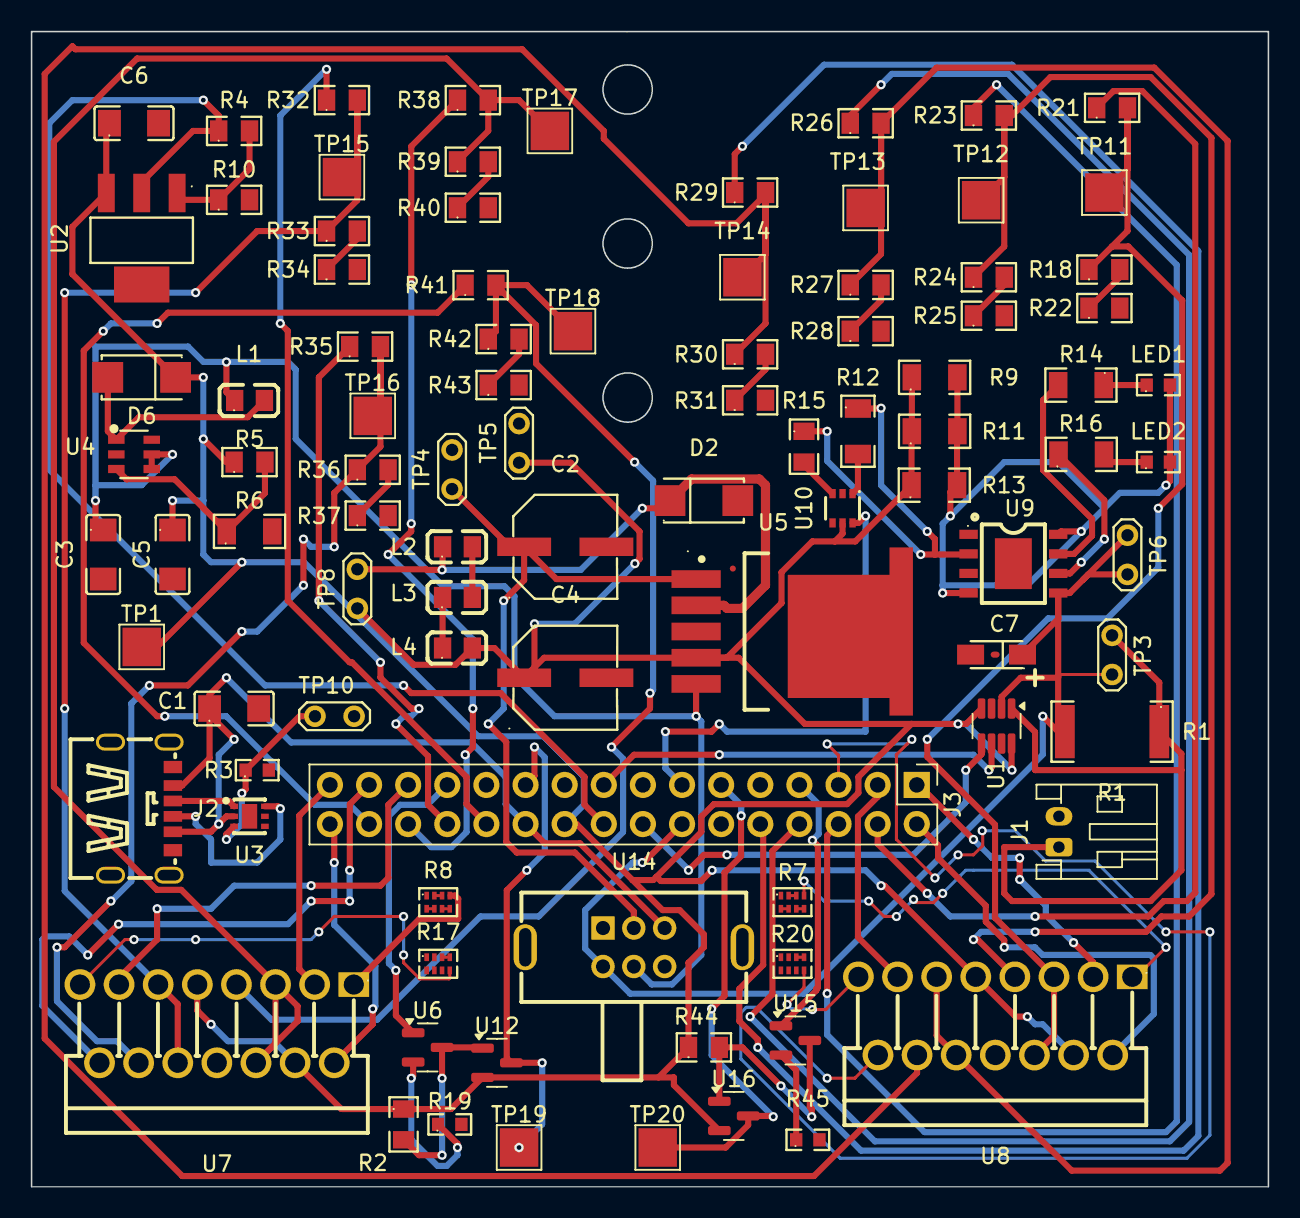
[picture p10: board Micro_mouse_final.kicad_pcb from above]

Board: 2 copper layers, 80.3 x 75.0 mm, 94 parts (0 on the bottom side), 80 nets.

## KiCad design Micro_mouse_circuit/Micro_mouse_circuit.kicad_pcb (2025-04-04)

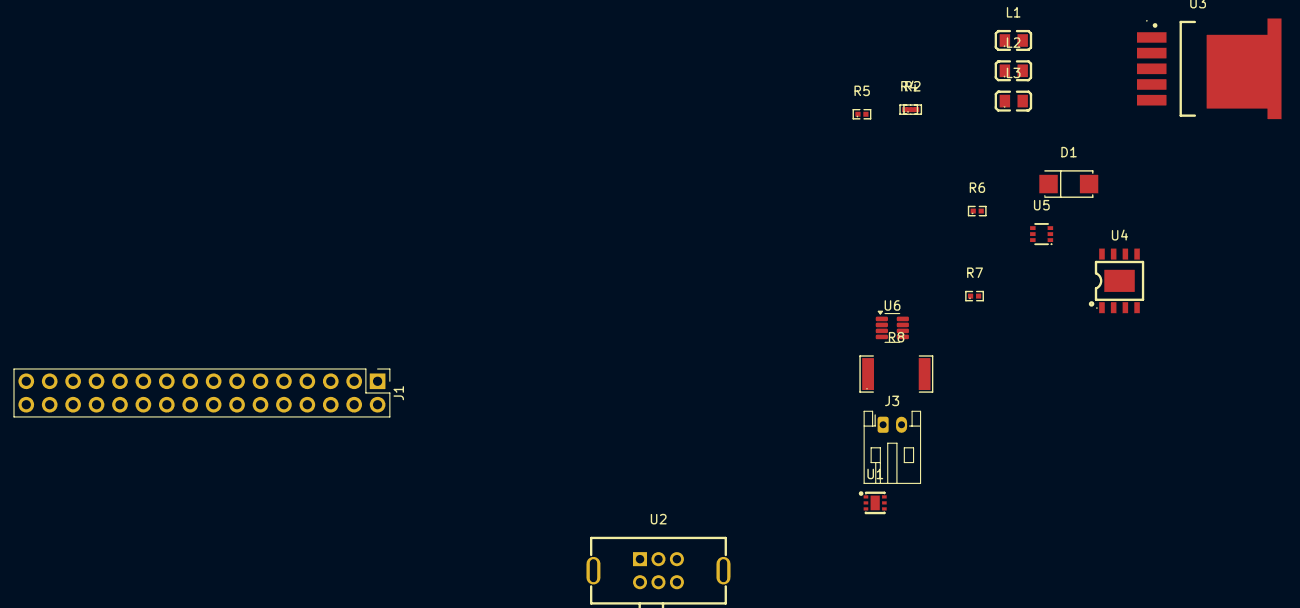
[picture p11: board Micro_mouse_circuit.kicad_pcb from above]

Board: 2 copper layers, 18 parts (0 on the bottom side), 18 nets, no tracks yet.

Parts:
D1: SS34_C8678; SMA_L4.3-W2.6-LS5.2-RD
J1: Conn_02x16_Odd_Even; PinHeader_2x16_P2.54mm_Vertical
J3: Conn_01x02; JST_PH_S2B-PH-K_1x02_P2.00mm_Horizontal
L1, L2, L3: 10uH; L0805
R2, R6: 2k; R0402
R4, R5: 1k; R0402
R7: 6k; R0402
R8: 0.2A; R2512
U1: HUSB237-AA001-DN06R; TDFN-6_L2.0-W2.0-P0.65-TL-EP
U2: SK22D15L5; SW-TH_XKB_SK22D15L7
U3: LM2596SX-5_0/NOPB; TO-263-5_L10.2-W8.9-P1.70-TL
U4: TP4056_C382139; ESOP-8_L4.9-W3.9-P1.27-LS6.0-BL-EP
U5: SN74LVC1G3157DCKR; SC-70-6_L2.2-W1.3-P0.65-LS2.1-BR
U6: INA219AxDCN; SOT-23-8

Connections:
5V: L1.2, R2.1, U3.4 (FB), U4.8 (CE), U6.4 (VS), U6.8 (A1)
9V: J1.22, U1.2 (VUSB), U2.2, U3.1 (VIN)
/FAST_CHARGE_CTRL: J1.13, U5.6 (S)
/I2C1_SCL: J1.16, U6.5 (SCL)
/I2C1_SDA: J1.17, U6.6 (SDA)
/R_prog: R6.1, R7.1, U4.2 (PROG)
Battery: J1.14, U4.5 (BAT)
GND: D1.2 (A), J1.19, J1.23, J3.2, U1.7 (GND), U3.3 (GND), U3.5 (ON#/OFF), U3.6 (GND), U4.1 (TEMP), U4.3 (GND), U5.2 (GND), U6.3 (GND), U6.7 (A0)
unnamed: D1.1 (K), L2.1, U3.2 (OUTPUT)
unnamed: J3.1, R8.1
unnamed: L1.1, L3.1
unnamed: L2.2, L3.2
unnamed: R5.2, U4.7 (CHRG#)
unnamed: R4.1, U4.6 (STDBY#)
unnamed: R2.2, U4.4 (VCC)
unnamed: R7.2, U5.3 (B1)
unnamed: R6.2, U5.1 (B2)
unnamed: R8.2, U6.1 (IN+)

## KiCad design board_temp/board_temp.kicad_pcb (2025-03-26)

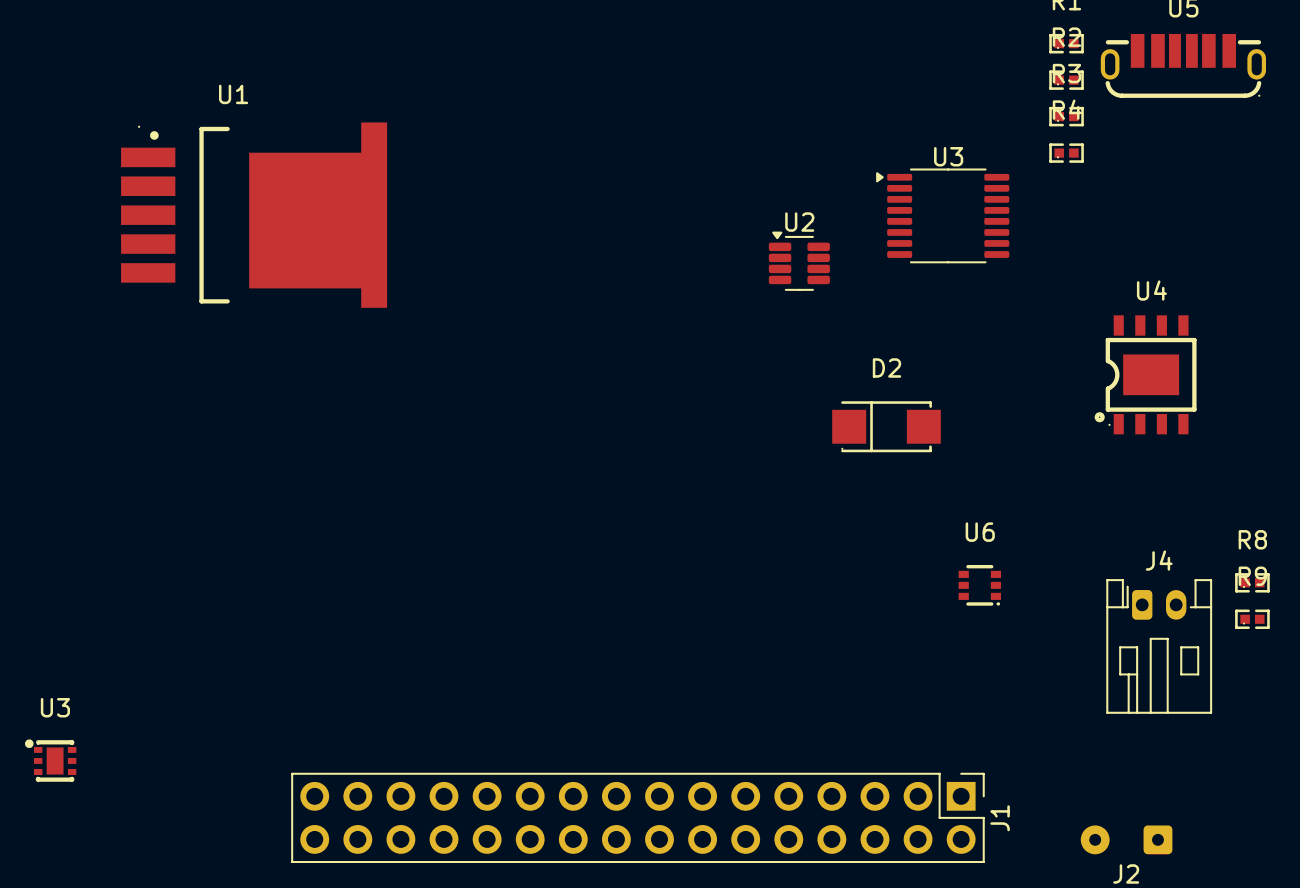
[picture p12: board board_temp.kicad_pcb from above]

Board: 2 copper layers, 17 parts (0 on the bottom side), 13 nets, no tracks yet.

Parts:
D2: SS34_C8678; SMA_L4.3-W2.6-LS5.2-RD
J1: Conn_02x16_Odd_Even; PinHeader_2x16_P2.54mm_Vertical
J2: Battery input; SolderWire-0.127sqmm_1x02_P3.7mm_D0.48mm_OD1mm
J4: Conn_01x02; JST_PH_S2B-PH-K_1x02_P2.00mm_Horizontal
R1, R2, R8: 2k; R0402
R3, R4: 1k; R0402
R9: 6k; R0402
U1: LM2596SX-5_0/NOPB; TO-263-5_L10.2-W8.9-P1.70-TL
U2: INA219AxDCN; SOT-23-8
U3: HUSB237-AA001-DN06R; TDFN-6_L2.0-W2.0-P0.65-TL-EP
U3#2: IP2721; TSSOP-16_4.4x5mm_P0.65mm
U4: TP4056_C382139; ESOP-8_L4.9-W3.9-P1.27-LS6.0-BL-EP
U5: TYPE-C_6P_LTH6_5; USB-TYPE-C-SMD_TYPE-C-6P-LTH6.5
U6: SN74LVC1G3157DCKR; SC-70-6_L2.2-W1.3-P0.65-LS2.1-BR

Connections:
9V: J1.22, U1.1 (VIN), U3.2 (VUSB)
/I2C1_SCL: J1.16, U2.5 (SCL), U2.7 (A0)
/I2C1_SDA: J1.17, U2.6 (SDA), U2.8 (A1)
/R_prog: R8.1, R9.1, U4.2 (PROG)
/fast_charge: J1.13, U6.6 (S)
Buck_22: R2.1, U1.4 (FB), U4.8 (CE)
GND: D2.2 (A), J2.2, R1.1, U1.3 (GND), U1.5 (ON#/OFF), U1.6 (GND), U2.3 (GND), U3.7 (GND), U4.1 (TEMP), U4.3 (GND), U6.2 (GND)
unnamed: D2.1 (K), U1.2 (OUTPUT)
unnamed: R4.2, U4.7 (CHRG#)
unnamed: R3.1, U4.6 (STDBY#)
unnamed: R2.2, U4.4 (VCC)
unnamed: R9.2, U6.3 (B1)
unnamed: R8.2, U6.1 (B2)

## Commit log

2025-03-25 changed charging config
    [board_temp.kicad_pcb, board_temp.kicad_sch, rough BoM.xlsx]
2025-03-26 reorganized some files
    [board_temp.kicad_sch]
2025-03-26 added USB PD
    [board_temp.kicad_pcb, board_temp.kicad_sch, rough BoM.xlsx]
2025-03-26 began schematic rev 3.0
    [Micro_mouse_circuit.kicad_pcb, Micro_mouse_circuit.kicad_sch, board_temp.kicad_pcb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]
2025-03-26 adding footprint libraries
    [Micro_mouse_circuit.kicad_pcb, Micro_mouse_circuit.kicad_sch, rough BoM.xlsx]
2025-03-27 assigned additional footprints
    [Micro_mouse_circuit.kicad_pcb, Micro_mouse_circuit.kicad_sch, rough BoM.xlsx]
2025-03-28 4AM version of this circuit
    [Micro_mouse_circuit.kicad_sch]
2025-03-28 Board System 5
    -Includes block desegnations
    [Micro_mouse_circuit_V5.kicad_sch]
2025-04-04 02/28 submission
    [BOM-Micro_mouse_final.csv, Micro_mouse_circuit.kicad_pcb, Micro_mouse_circuit_V5.kicad_pcb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]
2025-04-07 common share
    [Micro_mouse_final.kicad_pcb, Micro_mouse_final.kicad_sch]
2025-04-07 push - kt
    [Micro_mouse_final.kicad_pcb, Micro_mouse_final.kicad_sch]
2025-04-07 Max Half - PCB Board V6
    -Version before 2.4V regulation of motor control
    -Version before master kill switch
2025-04-09 FInal Additions to Schematic
    -Added Kill Switch
    -Moderated 3.3 Motor Control to 2.4 V
    [Micro_mouse_final.kicad_pcb, Micro_mouse_final.kicad_sch]
2025-04-09 push to Max - switch config finalized
    [BOM-Micro_mouse_final.csv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]
2025-04-09 common share update
    [Amp setup.kicad_sch, BOM-Micro_mouse_final.csv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]
